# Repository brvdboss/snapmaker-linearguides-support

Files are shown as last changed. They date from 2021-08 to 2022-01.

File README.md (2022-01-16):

# Adapters for linear guides for the Snapmaker 2.0
 To reduce the wobbling of the build plate I have installed linear guides that provide additional support. These adapters help to connect the guides to the buildplate.

 Especially when doing cnc tasks, the buildplate can be pushed down by the toolhead. This results in less accurate work and may reduce the quality of your work. Some people also report some instability of the platform in general. However, this can vary between different devices.

 A wonderful job was already done by [3DNate](https://www.thingiverse.com/3dnate/) with this design: https://www.thingiverse.com/thing:4860729
 The only drawback, you need to accurately measure the the height, print and make sure it fits and/or create intermediate pieces to the exact needed height. I wanted to make this adjustable so it's easier to install and use.

 Therefore a simple design was created with a nut that can be adjusted. Similar to how a lot of tables can be leveled by turning one of the feet into a higher or lower position.

 I have used an SBR-16 linear rail for my modification. If you are using another type of rail, you may need to make some adjustments.

## Why use this?
To provide extra support to the build plate.
Note, this is no replacement for tramming your machine (i.e. especially make sure both vertical axis are aligned to the horizontal plane). That still needs to be done reliably.

## Overview of elements
- **bottomwiththread**: The bottom part that is mounted to the guide that rolls over the rail.  You need 4 of these.
- **bottomfiller**: The guide has a small cutout, this fills that cutout to provide extra support.  This could have been combined with the bottomwiththread, but then you would need supports which I wanted to avoid. You need 4 of these.
- **nut**: The nut that screws onto the thread and thus pushes upwards. There are holes in the side to allow putting in a screw to fixate in a final position or put in a drup of glue. Probably not needed to fixate it that way.
- **railtopwithhole**: a remix of the design by 3Dnate to "grab" the Snapmaker carriage. You need 4 of these. It's not strictly necessary, but if you want to make sure the holes are aligned you should mirror 2 of them. If you have a new style of bed for the snapmaker (the design has been revised) it should be possible to replace that stl to generate a fitting part for your needs.
- **wrench**: The clearance between the bed & adapter is rather small which means most standard wrenches (or fingers for that matter :) ) won't fit between. this thin wrench does.

Where possible all objects are parameterized so they can easily be adjusted.
Holes are foreseen so the set screws to adjust the guides are accessible.

## What to watch out for when using this
- These are not a replacement for tramming your machine 

## How to print
Make sure to print the threads with a high quality setting. I have had great success with a variable layer height in Prusaslicer to get a good balance between speed and quality. (threaded parts with a layer height of 0.08 to 0.12, other parts of the print with a layer height of 0.30).

After printing and putting the nut on the thread, don't force it. The tolerance is low, if you feel too much resistance, unscrew a bit, tighten again just a bit further, unscrew etc.  Repeat that until it fits perfectly and you can easily tighten and loosen the nut.

## Result
In action: https://youtu.be/2wn5efR2PGg

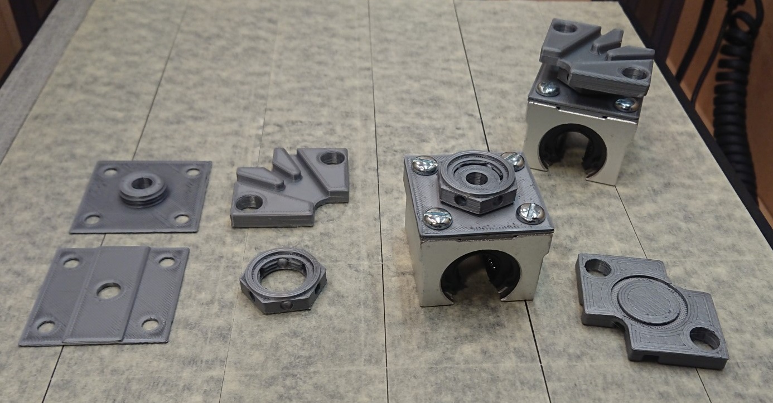
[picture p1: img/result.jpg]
printed result Printed result
printed result: 

## Other
There are some alternative approaches in the OpenScad file using more of a type jack wrench approach, however, there was too little clearance between the rail and buildplate to make this work. Those are still in the code, but lack a bit of documentation.  The relevant code for the third and final iteration is at the bottom of the file. (look for "third and final iteration")

To generate the threaded parts, I've made use of the excellent [threadlib](https://github.com/adrianschlatter/threadlib) library, put that in a "threadlib" folder in the source directory to build the project.

This thing is also published on Thingiverse: https://www.thingiverse.com/thing:4935804

**Warning if you have the new bed**
The version for the new bed does not provide enough clearance to install it.  A possible workaround is to insert spacers between the y-rail and bed.

I've had a chance to get a better look at the new platform as someone has taken the time to model it which makes it a lot easier to inspect it without having it physically:
https://cults3d.com/en/3d-model/tool/snapmaker-2-0-platform-3d-model-a250-a350-a350t

If you look at the files for the new and old model, it becomes very clear that the new model is thicker/higher than the old one. (the pointy ends especially)

And it is that 3mm that we're missing indeed.  If I make the top part thin enough, it falls apart as the different segments are no longer connected :(  So coming up with a solution will be more complex than just shaving off a part.
Something that, in all honesty, I won't be doing just for fun as I have other projects lined up right now.  And not being able to test it myself makes that a pain.

It should be doable however:
* the bottom part could be reduced to just fill the recess skipping the holes to attach it. it will stay in place just because of the pressure and it is only there to provide some support. That will save 1mm.
* the threaded part and screw could both lose 1mm as well. if needed. (perhaps remove the holes in the nut to make sure it stays strong enough).  with that I think it's also possible to shave up 1.5-2mm which should bring it in range of what's needed.

If someone wants to make these necessary changes I'll be happy to explain the OpenScad code if needed to get you started.
**End Warning**

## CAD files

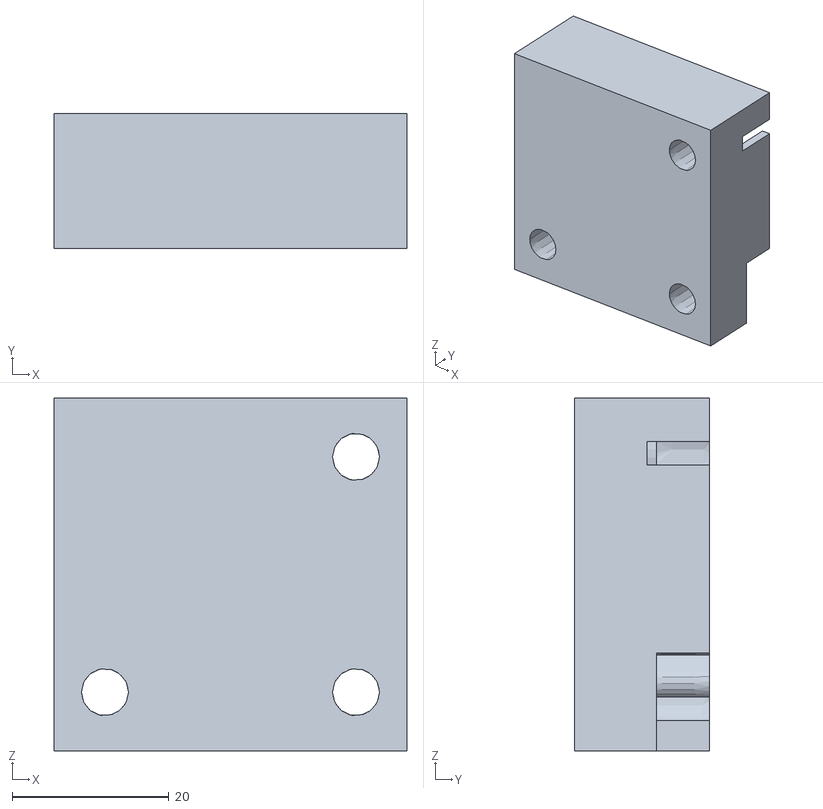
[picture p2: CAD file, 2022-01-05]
src/Linear_Rail_Adapter_v4.stl
45.0 x 17.2 x 45.0

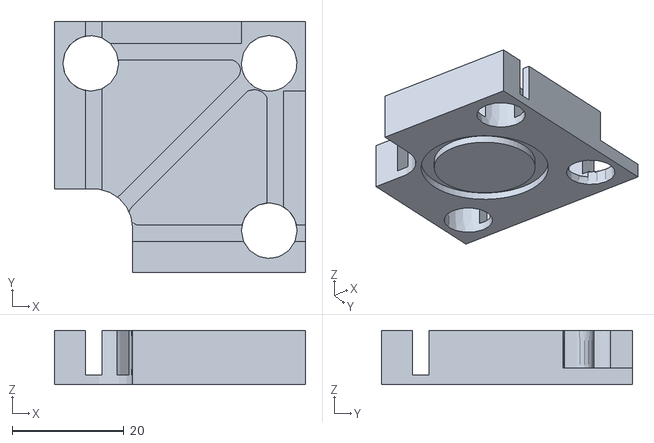
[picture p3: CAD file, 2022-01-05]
stl/railtopwithhole_newbed.stl
45.0 x 45.0 x 9.75

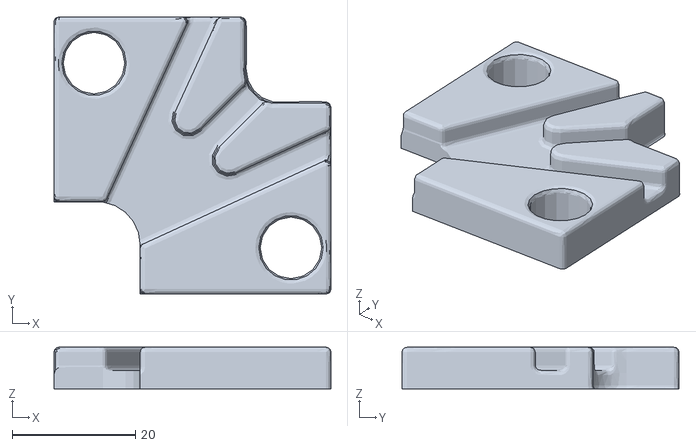
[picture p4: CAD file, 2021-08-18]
stl/railtopwithhole.stl
45.0 x 45.0 x 6.75

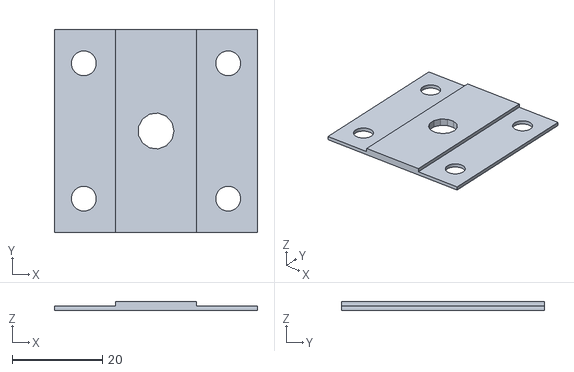
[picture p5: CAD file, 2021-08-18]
stl/bottomfiller.stl
45.0 x 45.0 x 2.00

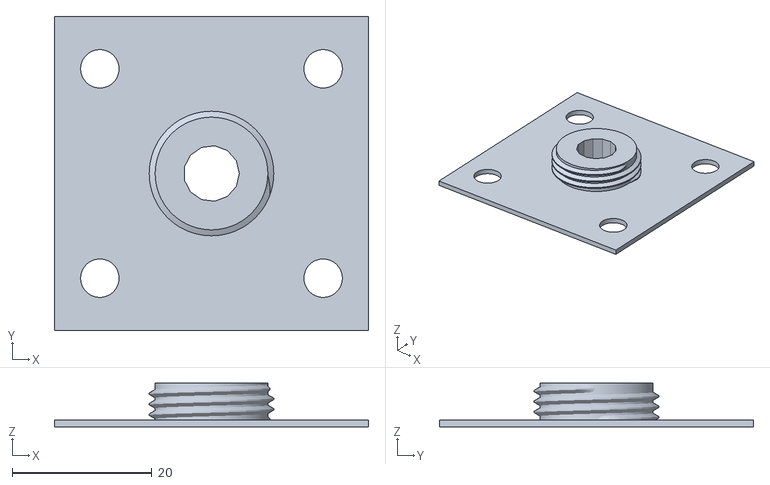
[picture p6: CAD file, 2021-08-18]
stl/bottomwiththread.stl
45.0 x 45.0 x 6.25

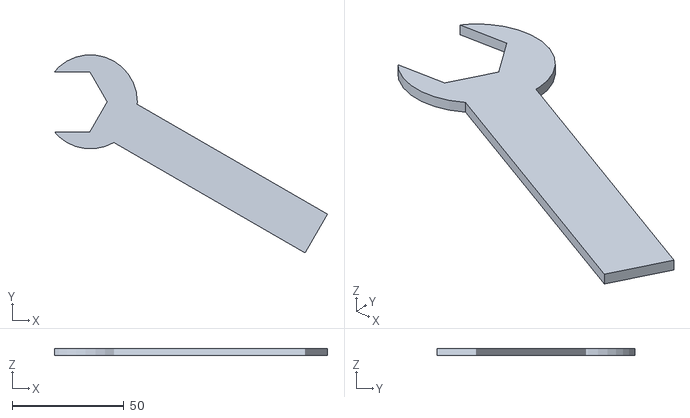
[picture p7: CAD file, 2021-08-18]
stl/wrench.stl
121.9 x 88.4 x 3.00

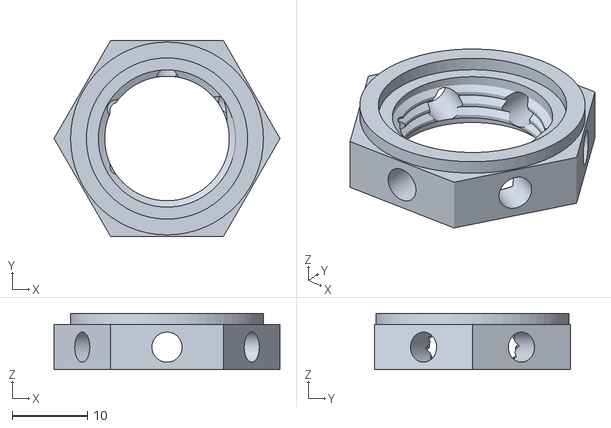
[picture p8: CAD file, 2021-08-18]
stl/nut.stl
30.0 x 26.0 x 7.50

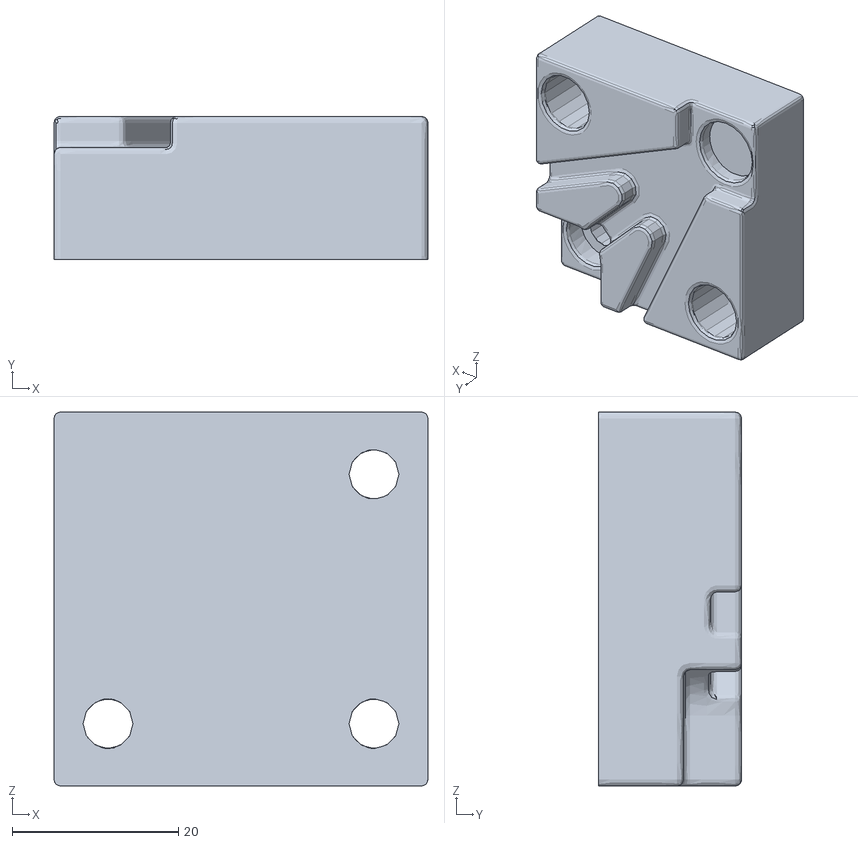
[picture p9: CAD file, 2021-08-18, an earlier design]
src/Linear_Rail_Adapter_v3.stl
45.0 x 17.2 x 45.0

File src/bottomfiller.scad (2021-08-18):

include <lib/wedge.scad>

bottomfiller();

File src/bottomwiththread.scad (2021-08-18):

include <lib/wedge.scad>

bottomwiththread();

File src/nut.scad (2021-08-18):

include <lib/wedge.scad>

threadedtube();

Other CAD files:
src/railtopwithhole.scad
src/wrench.scad

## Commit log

2021-08-18 Initial commit
    Saving this for posterity
    [Linear_Rail_Adapter_v3.stl, bottomfiller.scad, bottomfiller.stl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]
2022-01-05 Add version for new bed
    Add version for new bed.
    Untested. Note that this is 3mm thicker, so I'm not sure if it actually fits. For now assuming the v4 adapter for the new bed actually slides deeper into the bed. To be confirmed by a user that actua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
    [Linear_Rail_Adapter_v4.stl, railtopwithhole.scad, railtopwithhole_newbed.stl]
2022-01-05 Update README.md
    add warning about version for new bed
2022-01-16 Update README.md
    add warning for new bed users
